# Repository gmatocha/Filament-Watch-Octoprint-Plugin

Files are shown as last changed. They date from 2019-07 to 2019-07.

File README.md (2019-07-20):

# Filament Watch Octoprint Plugin

Initial work based on the [Filament Watch](https://github.com/rllynch/filament_watch) plugin by RLLynch.
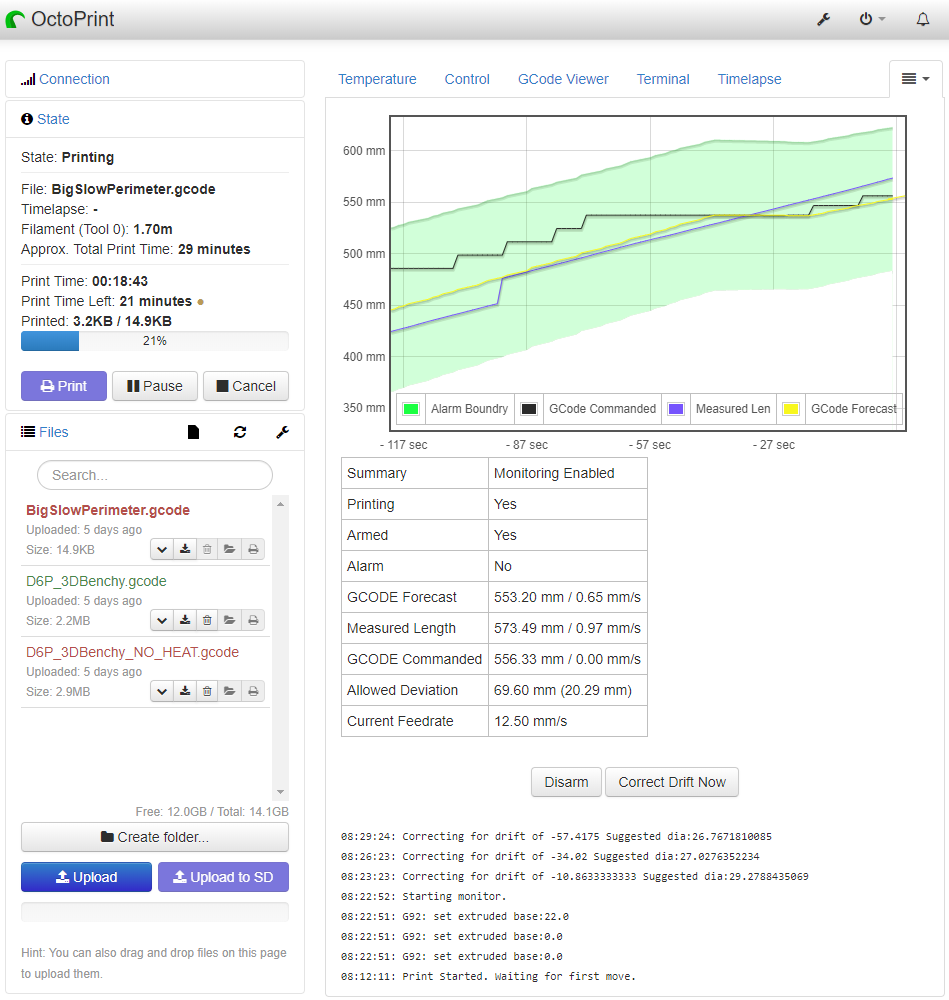
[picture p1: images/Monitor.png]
Monitor


[Are you sure you want to do this? ;)](#using-filament-watch---reliably)

## Features

* Pause, cancel, or just send GCODE when filament stops
* Automatic search for attached Arduino/rotary encoder
* Adjustable alarm boundaries
* USB connection to Octoprint/Octopi
* Helper functions for other plugins that might want access to extrusion data. [Docs](https://github.com/gmatocha/Filament-Watch-Octoprint-Plugin/blob/master/README_HELPER.md)

## Required sensor

Using this plugin requires a rotary encoder sensor, and an Arduino micro controller to manage the encoder. The enclosure STL files are designed for a rotary encoder with a 38mm (dia) x 35.5mm body, 6mm shaft and capable of running on 5v. The pulses/revolution of the encoder is not very critical; the encoder is run in quadrature mode, so the rated P/R will be multiplied by four. So even with a 100 P/R encoder and a 23mm encoder wheel, the resolution would be under .2mm - more than enough for accurate monitoring.

* Note if you do use an encoder with other than 600P/R, the DPM value in the Arduino code needs to be modified. Future versions will make this configurable through Octoprint.

## Purchased Parts:

1. Quadrature encoder:
  * Verified: Signswise 600p/r Incremental Rotary Encoder Dc5-24v Wide Voltage Power Supply 6mm Shaft [[Amazon link]](http://www.amazon.com/gp/product/B00UTIFCVA?psc=1&redirect=true&ref_=oh_aui_detailpage_o09_s00)
* Pending verification: 
* Other encoders may work, providing you come up with a suitable enclosure.

2. Arduino controller supporting 5V and Serial over USB:
* Verified: Adafruit Metro Mini 328 - 5V 16MHz [[Adafruit link]](https://www.adafruit.com/product/2590) [[Pinouts]](https://learn.adafruit.com/adafruit-metro-mini/pinouts)

3. USB A to Micro-B cable for Arduino [[Adafuit link]](https://www.adafruit.com/product/592)

4. Optional: 2 x 0.1" pitch header blocks [[Adafruit link]](https://www.adafruit.com/products/2142)

5. Optional: (depending on case you use) 608 ball bearing [[Amazon link]](https://www.amazon.com/Groove-Bearing-Bearings-Skateboard-Printer/dp/B07FGVFN6F). These are the same bearings used in skates and skateboard wheels. You don't need anything fancy here - don't spend money on ceramic or high abec bearings. Old dead ones will work as long as they roll smoothly.

6. Optional: 30mm Rotary Encoder wheel [[Ali Express Link]](https://www.aliexpress.com/item/32974396980.html). The enclosure stl files below include a wheel stl that is designed for the enclosure, and is usually printed in a soft material like TPU/Ninjaflex. Manufactured wheels are higher quality, but generally not so much as to affect Filament Watch. If you do use a manufactured wheel, choose a case that is designed for it.

## Printed parts - Enclosures and wheels:

There are several options for the encoder housing, depending on what will work with your setup.

1. RLLynch's [base and wheel](http://www.thingiverse.com/thing:936521) and optional [mini metro enclosure](http://www.thingiverse.com/thing:936519)

2. [My housing for the D6](https://www.thingiverse.com/thing:3746948)

## Wiring

### Wiring instructions for the Metro Mini 328
  Optionally solder the header blocks first.
  (Note check your enclosure to see if it's compatible with the header blocks)

1. Encoder red (power) - 5V
2. Encoder black (ground) - GND
3. Encoder green (output 1) - digital pin 3
4. Encoder white (output 2) - digital pin 2



## Installation

1. Install the plugin in Octoprint Settings->Plugin Manager:
* Manually using this URL: https://github.com/gmatocha/Filament-Watch-Octoprint-Plugin
* From the [Octoprint Plugin repositry](https://plugins.octoprint.org/) (pending)

2. Compile and flash Arduino/filament_watch/filament_watch.ino into the Metro Mini using either the Arduino IDE, or the command line scripts shown below:

3. Connect the Metro Mini by USB to the computer running OctoPrint. Attach the wheel to the encoder and place it in the base. Feed the filament through the base.

## Configuration

After installation, configure the plugin via OctoPrint Settings interface.
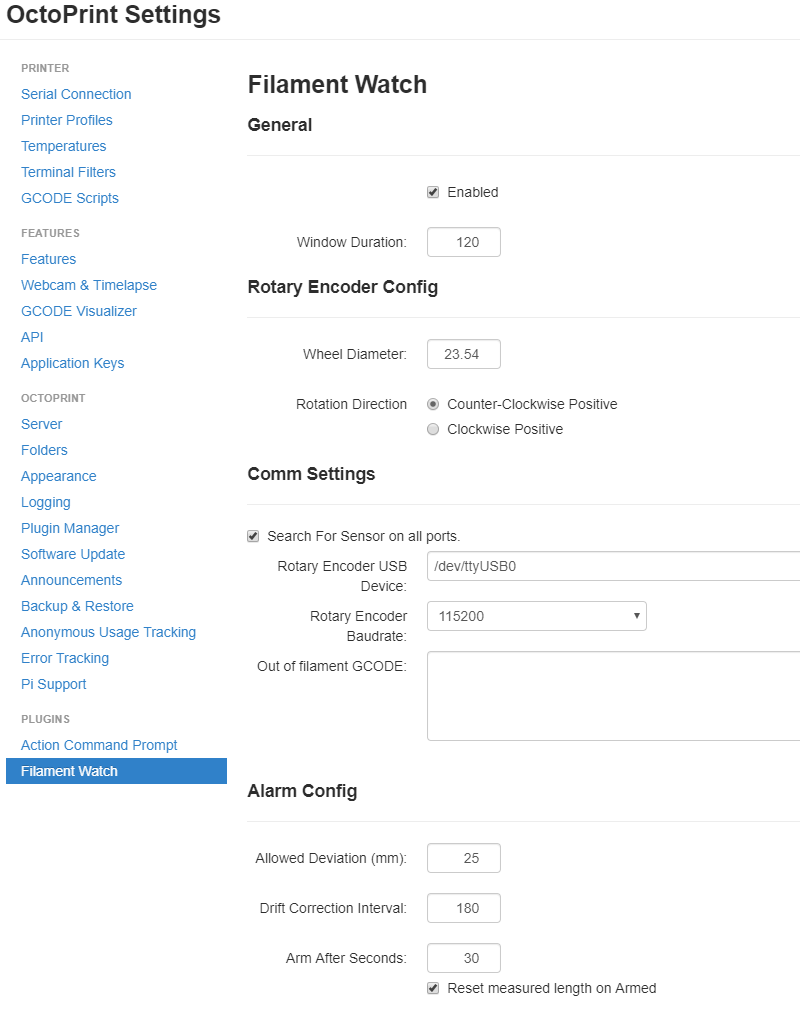
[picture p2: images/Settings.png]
Settings

* Allowed Deviation (mm): If monitored length is more or less than the forecast gcode, 

### Pause and Resume Scripts
In addition to preventing wasted filament after a feed problem, in many cases Filament Watch allows problems to be corrected without destroying the print in progress. To do this, you'll need to use OctoPrints GCODE Scripting feature to move the print head out of the way on pause, then return it to the exact same location when the print resumes.

Copy the scripts below into the **After print job is paused**, and **Before print job is resumed** fields in *Octoprint->Settings->GCODE Scripts*

###### Scripts below built from [here](https://community.octoprint.org/t/writing-a-resume-gcode-script-using-last-temperature/774/2), [here](https://community.octoprint.org/t/better-pause-function-in-octoprint/5331), and [the official scripting docs.](http://docs.octoprint.org/en/master/features/gcode_scripts.html?highlight=script#more-nifty-pause-and-resume). Thanks Gina and OutsoucedGuru for the excellent write-ups!

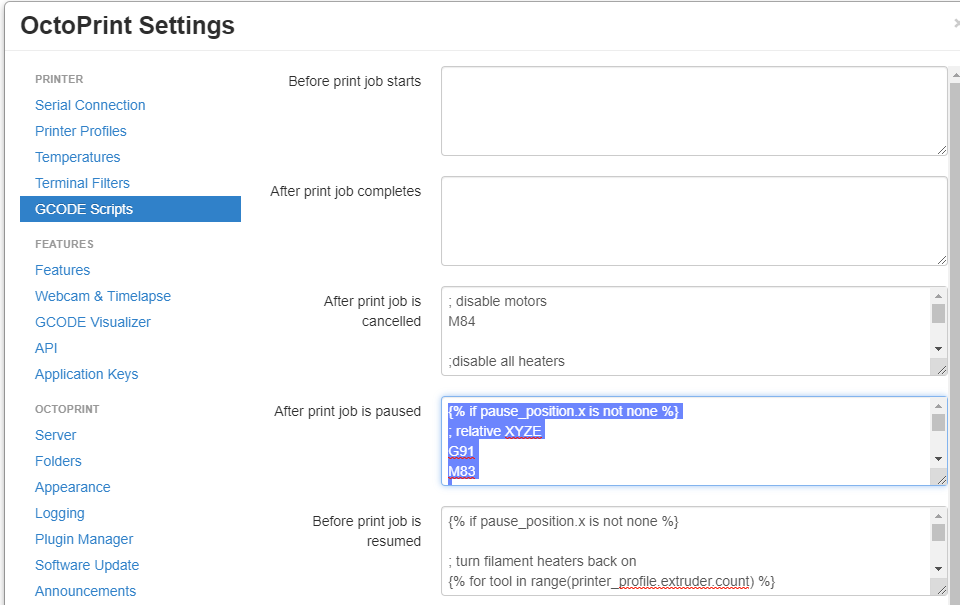
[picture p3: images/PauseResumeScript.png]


#### After print job is paused
```
; From 
{% if pause_position.x is not none %}
; relative XYZE
G91
M83

; retract filament, move Z slightly upwards
G1 Z+5 E-1.5 F4500

; absolute XYZE
M82
G90
; move to a safe rest position, adjust as necessary
G1 X0 Y0

; Home X and Y only
;G28 X Y

;disable heater, but not bed because we want to keep adhesion
{% snippet 'disable_hotends' %}

{% endif %}

; play a jaunty tune (if your printer speaks)
M300 S440 P1000
M300 S660 P1000
M300 S440 P1000
M300 S660 P1000
M300 S440 P1000
```

#### Before print job is resumed
```
{% if pause_position.x is not none %}

; turn filament heaters back on
{% for tool in range(printer_profile.extruder.count) %}
    {% if pause_temperature[tool] and pause_temperature[tool]['target'] is not none %}
        {% if tool == 0 and printer_profile.extruder.count == 1 %}
            M109 T{{ tool }} S{{ pause_temperature[tool]['target'] }}
        {% else %}
            M109 S{{ pause_temperature[tool]['target'] }}
        {% endif %}
    {% else %}
        {% if tool == 0 and printer_profile.extruder.count == 1 %}
            M104 T{{ tool }} S0
        {% else %}
            M104 S0
        {% endif %}
    {% endif %}
{% endfor %}

; relative extruder
M83

; prime nozzle
G1 E-5 F4500
G1 E5 F4500
G1 E5 F4500

; absolute E
M82
; absolute XYZ
;G90

; reset E
G92 E{{ pause_position.e }}

; move back to pause position XY
G1 X{{ pause_position.x }} Y{{ pause_position.y }} F1500
; then move back to pause position Z to minimize risk of bumping part off bed
G1 Z{{ pause_position.z }} F1500

; reset to feed rate before pause if available
{% if pause_position.f is not none %}G1 F{{ pause_position.f }}{% endif %}
{% endif %}
```

## Using Filament Watch

### The Graph:
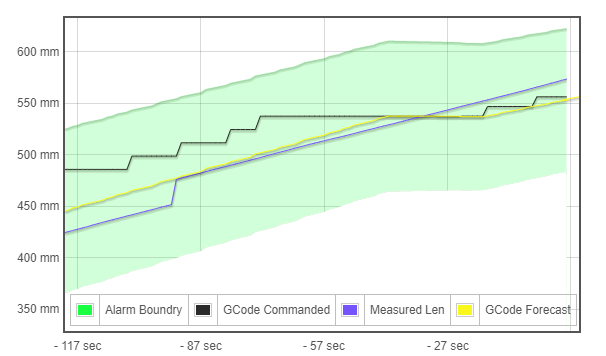
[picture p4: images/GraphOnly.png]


The graph on the Filament Watch tab shows four values:
* GCODE Commanded (black): This is the extruded length sent to the printer. Note it deviates from reality because of queuing and the time the printer takes to execute the moves. On large slow prints this deviation can be quite large.
* Measured Len (blue): This is the measurement from the rotary encoder, plus a drift correction that is applied on a regular interval (controlled by Drift Correction Interval in [settings](#Configuration)). You can see a drift correction here at -95 seconds. Drift Correction prevents false alarm triggers from accumulated small errors on large prints.
* GCODE Forecast (yellow): This is Filament Watch's best guess of how much filament has been extruded in real-time. This is the line that Filament Watch uses when determining whether an alarm condition has occurred.
* Alarm Boundary (green area): GCode Forecast +/- Allowed Deviation from [settings](#Configuration) plus an additional deviation allowance calculated from the difference between the GCODE Forecast and CGODE Commanded. If Measured Length goes outside this value, an alarm is triggered. Note this value is dynamic; after a wide deviation allowance is set, it will slowly (defaults to .1 mm/sec) return to the Allow Deviation value.

### Values Table

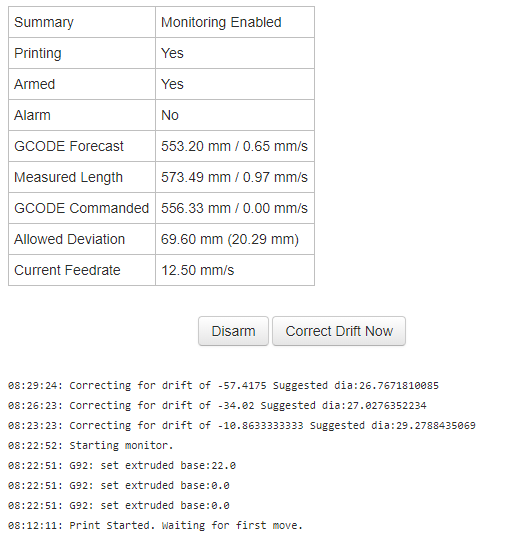
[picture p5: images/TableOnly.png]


 - Summary, Printing, Armed, and Alarm show the current state of Filament Watch.
 - GCODE Forecast, Commanded, and Measured length show the current values plotted on [the graph](#The_Graph:). The value after the slash is the instantaneous *extrusion rate* calculated over the last second. This can be useful when diagnosing under extrusion issues.
 - Allowed Deviation is the width of the Alarm Boundary. The value in parentheses is the current difference between Measured Length and the GCODE Forecast (ie, the current error).
 - Current Feedrate - the latest sent feedrate for the head (movement, not extrusion). Note this is the commanded rate, not the forecast rate, so it may not reflect reality at that moment in time. This can be useful when diagnosing under extrusion issues.

### Manual Buttons

 - Arm/Disarm - use this if you want to manually override the arm state while the print is running.
 - Correct Drift Now - causes drift correction (set Measured Length to GCODE Forecast value) to be applied immediately. Useful if you're getting close to alarming, but you know there are no print problems.

### Log
The section at the bottom shows the last 10 Filament Watch log lines, including drift corrections. See [](#Tuning) below.

## Tuning
As the print runs, Filament Watch will monitor accumulated errors and make suggestions for dialing in the exact rotary encoder diameter. Look for this value in the Filament Watch logs (circled below):

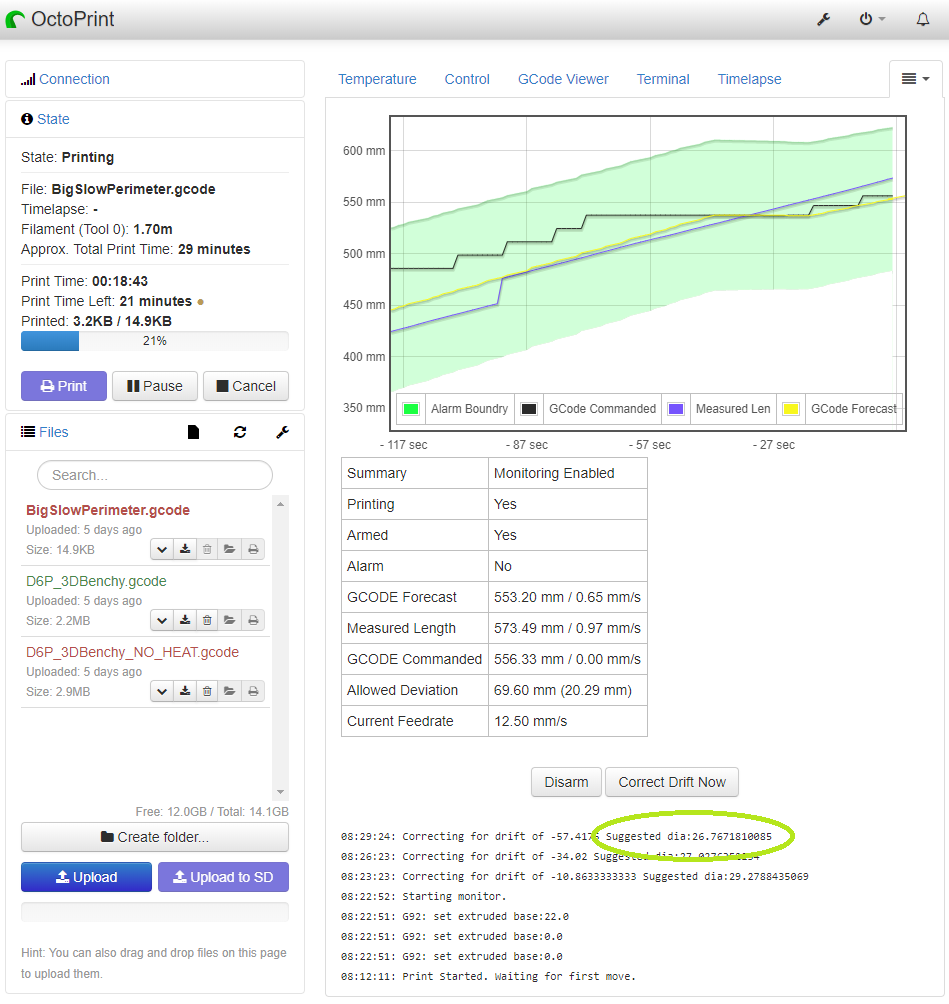
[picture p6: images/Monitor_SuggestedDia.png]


* At the beginning of the print, this suggested diameter will be way off, but will close in on the correct value the longer the print runs.
* Ironically, prints with many short moderately paced moves will produce a more accurate suggested diameter than prints with long slow extrusions. This is because forecasting must be used on the long slow prints, while short fast prints mean sent and measured lengths stay closer.

## Using Filament Watch - Reliably
I'll be honest with you...get ready.

You probably don't want to use Filament Watch. Boom.

Filament monitoring seems like a no-brainier right? *Throw in a rotary encoder....measure what moves and compare to what's supposed to move...simple right?*

Here's what they're not telling you. If the monitor is not **significantly *more*** reliable than your prints, it's worse than useless. Let's say 1 in 20 - 5% - of our prints fail because of a condition Filament Watch might detect (and since we're being honest - there are many it won't). Ok great, we can perhaps save half of those 1 in 20 prints. But if Filament Watch has the same error rate - false positive errors on 1 in 20 prints - then you will actually have MORE failed prints using Filament Watch even when it accurately detects true failures. For this reason Filament Watch has to be significantly more reliable than the printer itself to at least not be a hindrance. Throw in the fact that there are so many printers, so many different firmwares and motherboards with different caching buffer sizes and planning schemes, and so many physical configurations, and you start to get a sense of scale of this problem. But wait it gets worse - then there's the slicer, the print settings, and the model itself. 

All this means what Octoprint sends is almost never synchronized with the real world (which is what Filament Watch sees).
Sometimes it's not. even. close.

So is all lost? No, not at all. But expectations must be set.

#### Here are my suggestion for success with Filament Watch:
* Until you have Filament Watch dialed in, set Alarm Action [in settings](#Configuration) to GCODE only. Then set the GCODE script to nothing or just beep (if your printer speaks) to notify you of an alarm. Here're some beeps for Marlin based printers:
```
; Beeps
M300 S600 P700
M300 S400 P700
M300 S600 P700
```
    
* Don't rely on Filament Watch until you've verified it with the same or similar models. What does "similar" mean?
	- Same printer and slicer? Obviously
	- Similar speed? Yes
	- Same layer height? Yes
	- Similar model? Yes. Huh? Why the model itself? Because a Benchy with its small intricate moves will look very different to Filament Watch than a full volume cube, even with identical print settings.
	
* Wide alarm tolerances are OK. The difference between a 25mm alarm boundary and a 50mm boundary might only delay an alarm by 30 seconds...which won't make a difference between a salvageable and failed print. But it might prevent a false alarm that does fail the print.
* The same goes for the drift correction interval - a fast (say 120 second) drift correction might delay some alarms, but will make false alarms less likely.

#### Wow, that was all doom and gloom. Is there any reason TO use Filament Watch?

Yes. Obviously Filament Watch can and does detect out of filament, tangles, and clogged nozzles. **But it can also be an important diagnostic tool.** I've found some models (the Big Slow Perimeter file in the Parts\Test Parts directory, for example) that produce under-extrusion at some points in the model. On my D6, it will reliably under-extrude (extruder will skip steps) between 52% and 55% complete, and again on the last few percent. At this point it's printing slow (12.5mm/s moves) exterior walls at below 1mm/s extrusion rates. These defects are barely noticeable in the final print (until you know what to look for)...so they're not "failures", but I did learn something new about what my printer is actually doing. Now just to find a solution... ;)

Enjoy

<!--stackedit_data:
eyJoaXN0b3J5IjpbODk0MzE4MDczLDE3Njk2MzY5ODIsMzE3ND
Y5NDExLC0xNzU0NjcxMTAsLTg1ODQ4NjgyNywtMTcyNjk5MTMy
NSwxNTQyNDQ4NTExLDI4MTYxMDAyLC0xMTI4NzYyMTgxLC0xMj
YyNDYxOTE1XX0=
-->

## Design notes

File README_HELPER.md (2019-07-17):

# Filament Watch Helper Functions

## Function:
- **FilamentWatchExtrudedInfo**
## Returns:
Dictionary containing the following values:
- **gcodeExtrudedlLen** (float, mm):
	Latest extruded length per GCODE sent to the printer. Note, depending on queueing and planning in the printer, this length may not be acted upon for some time.
	
- **measuredExtrudedLen** (float, mm):
Current extruded length reading from the rotary encoder, plus drift correction.

- **gcodeForecastLen** (float, mm):
Filament Watches' best guess at the real current extruded length. This is what is used for comparisons to determine alarm conditions.

- **printing** (bool)
Whether there is a print in progress.

- **armed** (bool):
Whether Filament Watch Alarm has been armed. May be disarmed because the print hasn't run long enough yet, or manually disarmed by the user.
- **arm_alarm_in_sec** (int, seconds):
How many seconds until the alarm will arm. Will be 0 once armed, or if disarmed by the user.

- **alarm** (bool):
Whether Filament Watch has triggered an alarm.

- **paused** (bool):
Whether the print is paused.

- **alarmWindowWidth** (float, mm):
How far measuredExtrudedLen can be from gcodeForecastLen before triggering an alarm. The base for this number is the *Allowed Deviation (mm)* setting, plus the difference between commanded and forecast gcode. This widens the alarm window when there is large asynchronicity between sent gcode and the real world to prevent false alarms. This values decays back to Allowed Deviation at approximately .1mm/sec. 

<!--stackedit_data:
eyJoaXN0b3J5IjpbLTE5OTQxMDI4ODldfQ==
-->

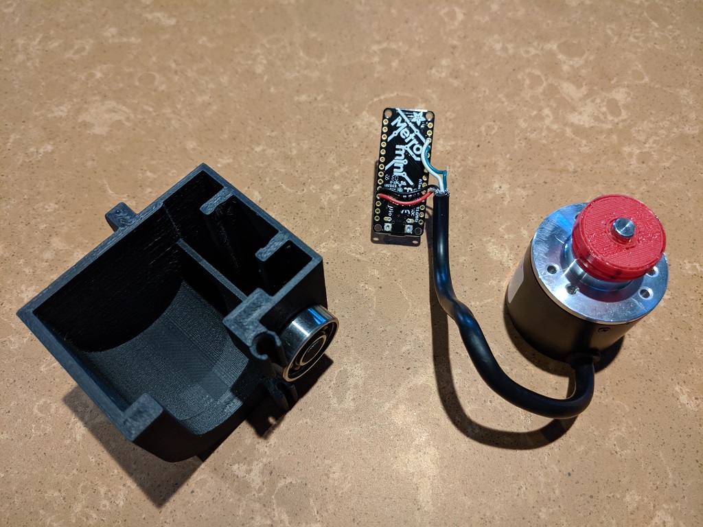
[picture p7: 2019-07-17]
images/Controller.jpg

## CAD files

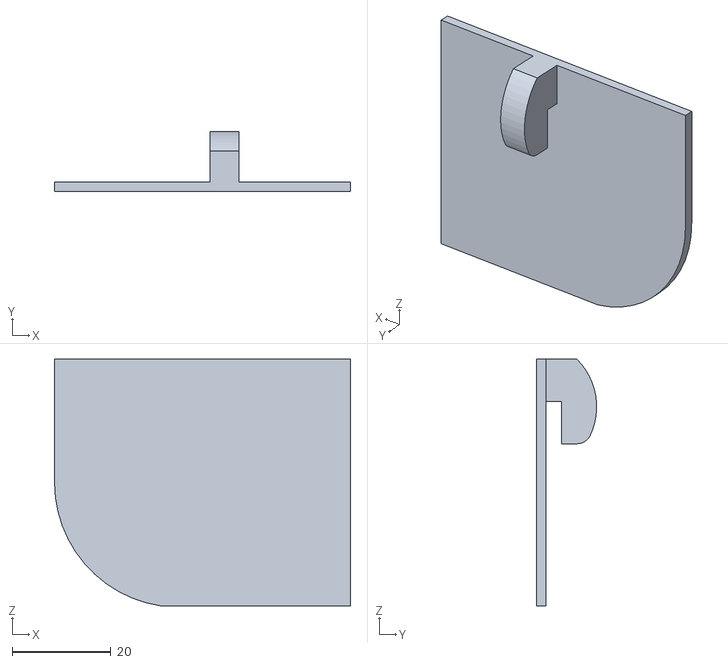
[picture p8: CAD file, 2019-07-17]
Parts/EncoderHolderMountingHook_ForD6_For23mmWheelBody.stl
60.0 x 12.2 x 50.0

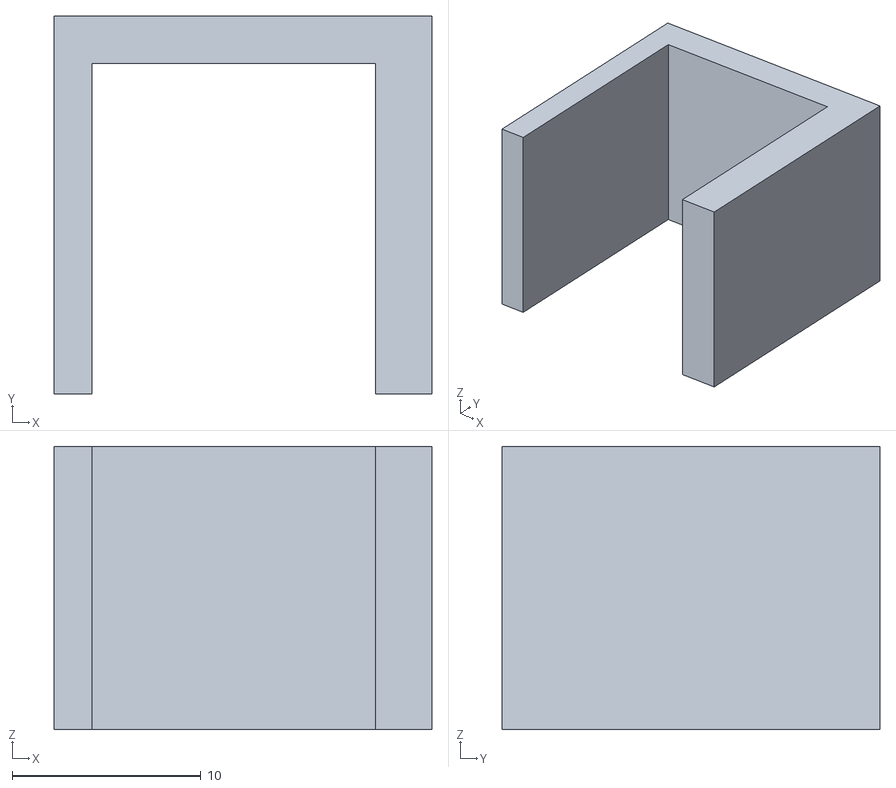
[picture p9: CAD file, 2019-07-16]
Parts/Test Parts/2-2.5-3x20x15mm.stl
20.0 x 20.0 x 15.0

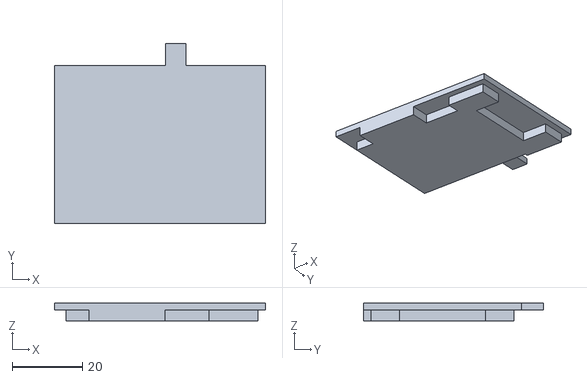
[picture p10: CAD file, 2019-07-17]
Parts/EncoderHolderLid_For23mmWheelBody.stl
60.0 x 51.2 x 5.00

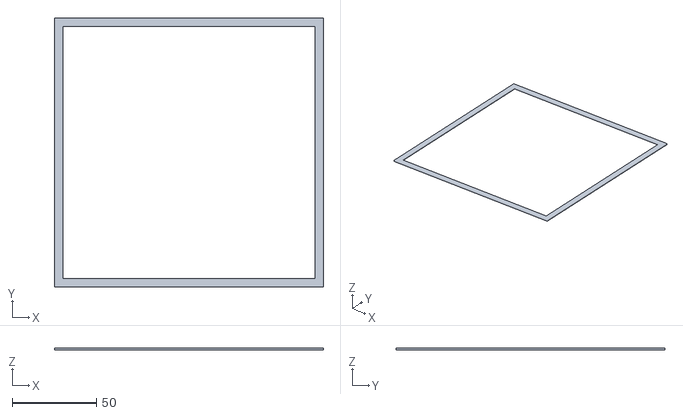
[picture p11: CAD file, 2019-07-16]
Parts/Test Parts/BigSlowPerimeter.stl
160.0 x 160.0 x 1

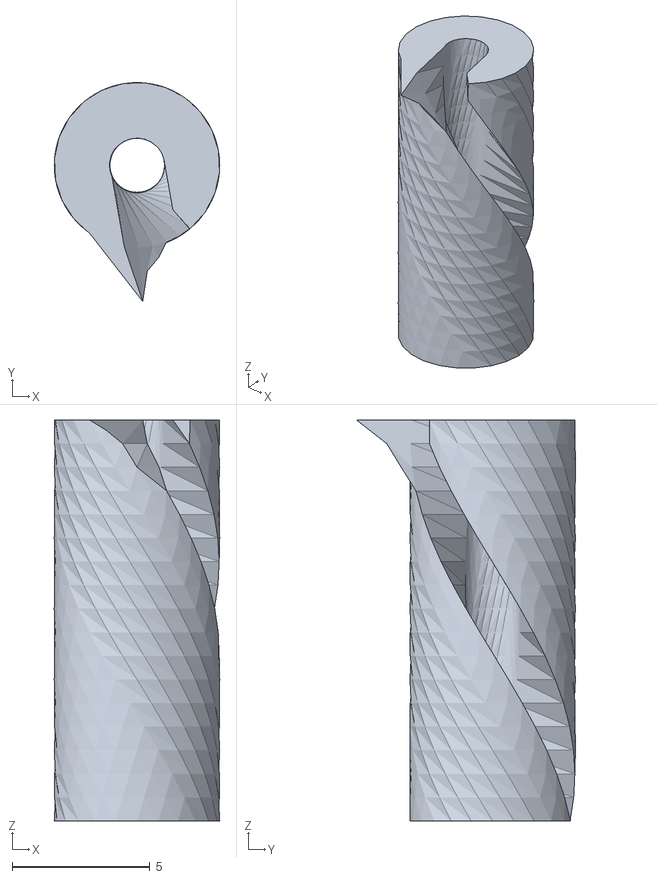
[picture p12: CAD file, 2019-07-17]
Parts/EncoderHolder_FilamentHelix.stl
6.00 x 7.94 x 14.5

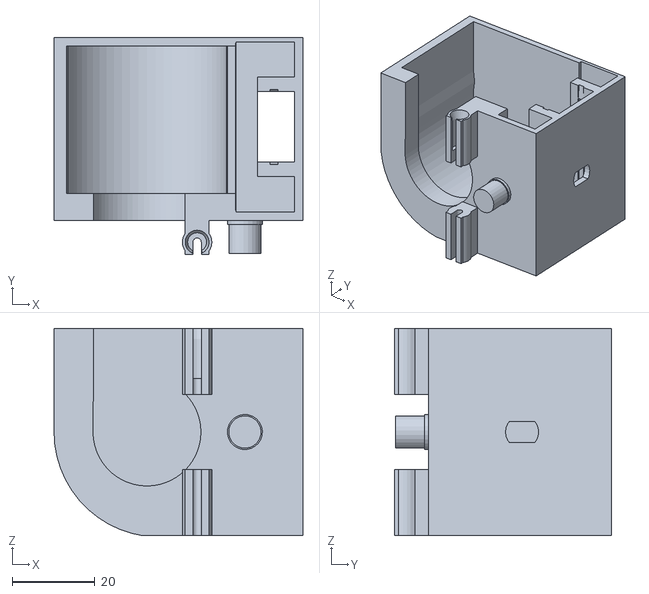
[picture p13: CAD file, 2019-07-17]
Parts/EncoderHolderBody_For23mmWheel_NoMounting.stl
60.0 x 52.2 x 50.0

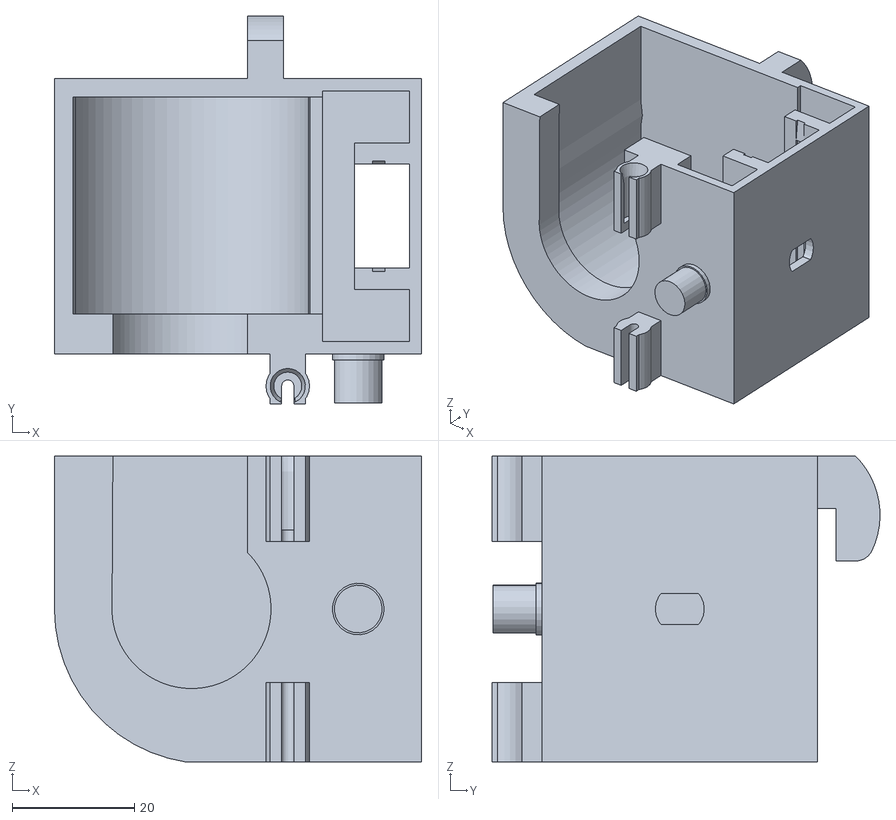
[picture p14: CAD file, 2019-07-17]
Parts/EncoderHolderBody_For30mmWheel_D6Mounting.stl
60.0 x 63.4 x 50.0

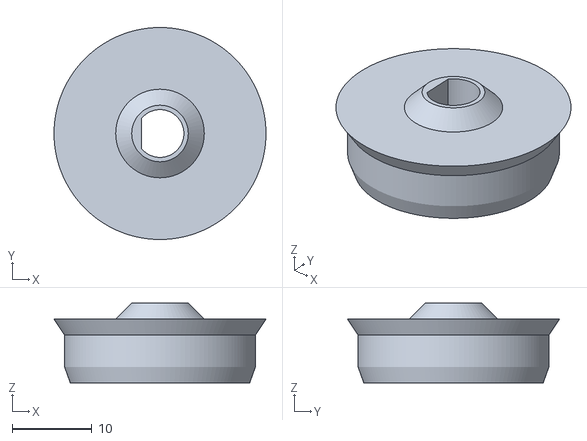
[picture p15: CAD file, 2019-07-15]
Parts/WheelRev3.stl
26.6 x 26.6 x 10.0

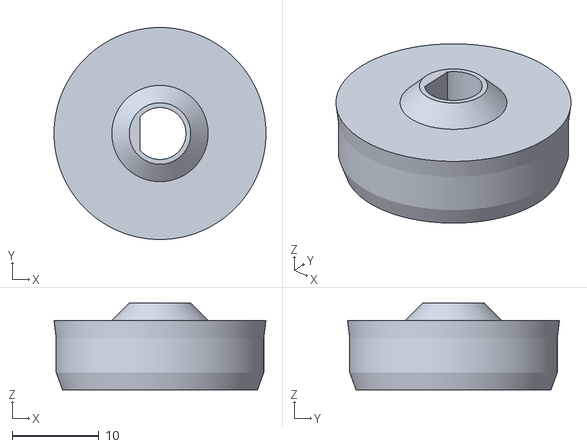
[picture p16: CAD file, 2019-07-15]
Parts/WheelRev3_NoLip.stl
24.5 x 24.5 x 10.0

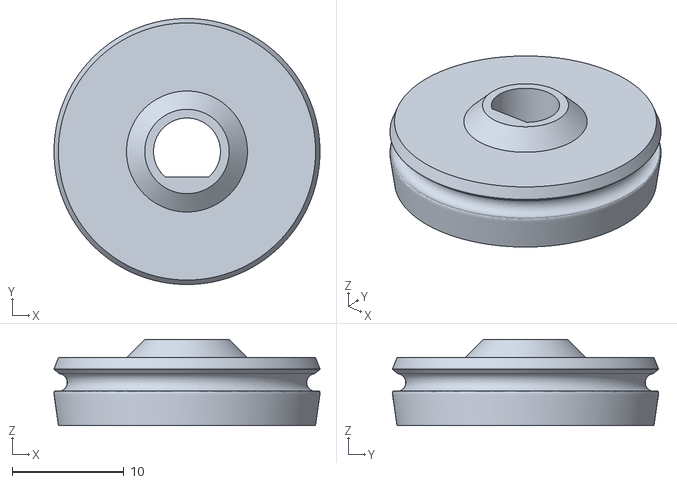
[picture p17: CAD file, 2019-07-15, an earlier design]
Parts/Wheel_Rev_2.stl
23.8 x 23.8 x 7.75

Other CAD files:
Parts/EncoderHolderBody.stl
Parts/EncoderHolderBody.skp
Parts/WheelRev2.skp

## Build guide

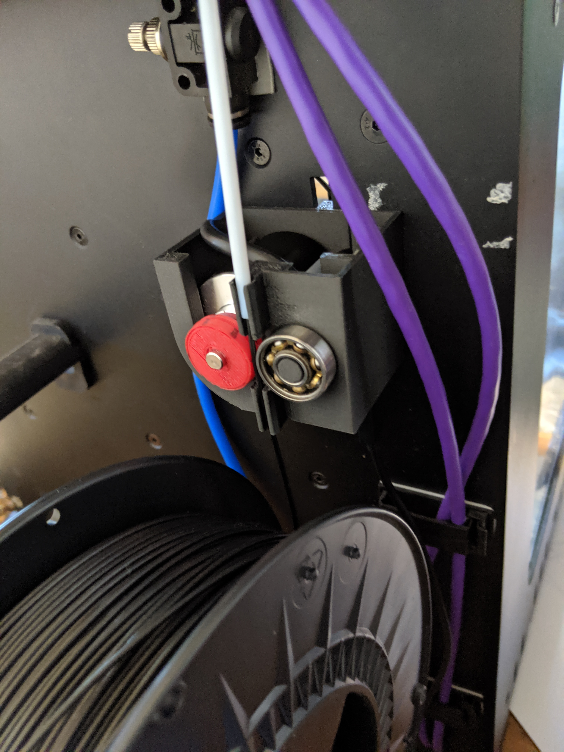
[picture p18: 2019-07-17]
images/OnPrinter.jpg

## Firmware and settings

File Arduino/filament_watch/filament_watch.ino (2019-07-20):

#define IN1 2
#define IN2 3

// in future versions this will be stored in EEPROM or flash to will persist after reboot
String ID = "NONE"; // 4 chars - set me as needed

int last_in1;
int last_in2;
int last_code;
long pos = 0;

int directionIncrementer = 1;
bool LoopingMode = false;
int LoopTimer = 1000;

bool ResultTypeMM = false; // false reports raw counter pos, true reports calculated mm traveled (requires WheelDia to be set)
float posScaler = 1.0;
int   DPR = 2400;
float WheelDia = 23.0;

String inputString = "";
bool stringComplete = false;

inline int decode(int in1, int in2)
{
  return (in2 << 1) | (in1 ^ in2);
}

inline void isr_common(int cur_in1, int cur_in2)
{
  int cur_code = decode(cur_in1, cur_in2);

  if (cur_code != last_code)
  {
    if (((cur_code + 1) & 3) == last_code)
      pos += directionIncrementer;
    if (((cur_code - 1) & 3) == last_code)
      pos -= directionIncrementer;

    last_code = cur_code;
  }

  last_in1 = cur_in1;
  last_in2 = cur_in2;
}

void isr1()
{
  int cur_in1 = digitalRead(IN1);
  int cur_in2 = last_in2;
  isr_common(cur_in1, cur_in2);
}

void isr2()
{
  int cur_in1 = last_in1;
  int cur_in2 = digitalRead(IN2);
  isr_common(cur_in1, cur_in2);
}

void setup() {
  // put your setup code here, to run once:
  pinMode(IN1, INPUT_PULLUP);           // set pin to input
  pinMode(IN2, INPUT_PULLUP);           // set pin to input
  Serial.begin(115200);
  while (!Serial) {
    ; // wait for serial port to connect. Needed for native USB port only
  }
  

  last_in1 = digitalRead(IN1);
  last_in2 = digitalRead(IN2);
  last_code = decode(last_in1, last_in2);

  attachInterrupt(0, isr1, CHANGE);
  attachInterrupt(1, isr2, CHANGE);
}

inline float CalcPos()
{
  if (ResultTypeMM)
    return pos * posScaler;
  else
    return pos;
}

void loop() {
  delay(100);
  String ReplyStr = "";

  if (stringComplete)
  {
    // This is is what we'll reply unless overriden below
    ReplyStr = "Set " + inputString;

    if (inputString == "FINDFILAMENTWATCH")
    {
      ReplyStr = "FilamentWatchHere!";
    }
    else if (inputString == "LOOP")
    {
      LoopingMode = true;
    }
    else if (inputString == "STOPLOOP")
    {
      LoopingMode = false;
    }
    else if (inputString == "DIRCWPOSITIVE")
    {
      directionIncrementer = 1;
    }
    else if (inputString == "DIRCCWPOSITIVE")
    {
      directionIncrementer = -1;
    }
    else if (inputString == "GETPOS")
    {
      ReplyStr = "FWPos ";
      ReplyStr = ReplyStr + CalcPos();
      ReplyStr = ReplyStr + " FWPos";
    }
    else if (inputString.startsWith("LOOPTIMEMS:"))
    {
      inputString.replace("LOOPTIMEMS:", "");
      LoopTimer = inputString.toInt();
    }
    else if (inputString.startsWith("SETWHEELDIA:"))
    {
      inputString.replace("SETWHEELDIA:", "");
      WheelDia = inputString.toFloat();

      ResultTypeMM = true;

      float cir = WheelDia * PI;
      posScaler = cir / float(DPR);
      pos = 0;
    }
    else if (inputString.startsWith("SETDPR:"))
    {
      inputString.replace("SETDRP:", "");
      DPR = inputString.toInt();

      float cir = WheelDia * PI;
      posScaler = cir / float(DPR);
      pos = 0;
    }
    else if (inputString == "RESULTTYPEMM")
    {
      ResultTypeMM = true;
      pos = 0;
    }
    else if (inputString == "RESULTTYPERAW")
    {
      ResultTypeMM = false;
      pos = 0;
    }
    else if (inputString == "RESETPOS")
    {
      pos = 0;
    }
    else if (inputString == "GETID")
    {
      ReplyStr = ID;
    }
    else if (inputString == "BLINK")
    {
      pinMode(LED_BUILTIN, OUTPUT);
      for (int i = 0; i < 3; i++)
      {
        digitalWrite(LED_BUILTIN, HIGH);
        delay(300);
        digitalWrite(LED_BUILTIN, LOW);
        delay(300);
      }
    }
    else if (inputString == "HELP")
    {
      Serial.println(F("FindFilamentWatch: produces 'FilamentWatchHere!' reply"));
      Serial.println(F("Loop:              Start sending measured pos every n ms. Set interval with LoopTimeMS"));
      Serial.println(F("StopLoop:          Stops looping"));
      Serial.println(F("LoopTimeMS:[ms]    Sets loop timer interval"));
      Serial.println(F("GetPos:            Gets current position"));
      Serial.println(F("ResultTypeMM       Returned values as mm traveled, and reset mm of travel to 0"));
      Serial.println(F("ResultTypeRaw      Returned values raw position and reset position to 0"));
      Serial.println(F("SetWheelDia:[mm]   Set diameter of the wheel for mm reporting. Also sets mode to ResultTypeMM"));
      Serial.println(F("SetDPR:[mm]        Set pulses per revolution (assuming quadrature encoding). Defaults to 2400"));
      Serial.println(F("DirCWPositive:     Set clockwise rotation positive"));
      Serial.println(F("DirCCWPositive:    Set counter clockwise rotation positive"));
      Serial.println(F("ResetPos:          Set position to 0"));
      Serial.println(F("GetID:             Get the 4 char ID for this device (defualt NONE)"));
      Serial.println(F("Blink:             Flash the LED"));
      ReplyStr = "";
    }
    else
    {
      ReplyStr = "Unrecognized Command:" + inputString;
    }


    if (ReplyStr.length())
      Serial.println(ReplyStr);

    stringComplete = false;
    inputString = "";
  }


  if (LoopingMode)
  {
    // taking out the 100 ms because we always delay 100 ms in this loop
    delay(LoopTimer - 100);

    ReplyStr = "FWPos ";
    ReplyStr = ReplyStr + CalcPos();
    ReplyStr = ReplyStr + " FWPos";

    Serial.println(ReplyStr);
  }

}

void serialEvent()
{
  while (Serial.available()) {
    // get the new byte:
    char inChar = (char)Serial.read();

    // if the incoming character is a newline, set a flag so the main loop can
    // do something about it:
    if (inChar == '\n')
    {
      inputString.toUpperCase();
      stringComplete = true;
    }
    else
    {
      // add it to the inputString:
      inputString += inChar;
    }

  }
}

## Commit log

2019-07-15 Initial Commit
    Filemanet Watch as an Octpprint plugin, based on RLLynch's work.
    [EncoderHolderBody.skp, EncoderHolderBody.stl, WheelRev2.skp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]
2019-07-16 added test models
    [2-2.5-3x20x15mm.stl, BigSlowPerimeter.stl]
2019-07-17 Additional holder parts
    [EncoderHolderBody.skp, EncoderHolderBody_For23mmWheel_NoMounting.stl, EncoderHolderBody_For30mmWheel_D6Mounting.stl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]
2019-07-17 oops...messed up a directory name
    [EncoderHolderBody.skp]
2019-07-20 fixed DPR error that caused compile error
    [filament_watch.ino]
